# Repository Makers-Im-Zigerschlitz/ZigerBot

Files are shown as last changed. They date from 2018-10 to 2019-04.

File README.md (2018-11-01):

# ZigerBot

Arduino shield to teach STEM / basic robotics

Current state: _planning_ 

## Goal

Create an Arduino(R) shield to help teach STEM / basic robotics

## General idea

We love teaching about mechanics, electricity, electronics and robotics. ZigerBot allows us to have a robust platform to teach the very basic of all this. Participants build their own robotic platform, solder the ZigerBot shield and connect both. ZigerBot can then be programmed via Arduino IDE or ArduBlockly .

## Inspiration
https://github.com/FuzzyNoodle/Fuzzy-Naked-Mega

## Features for first iteration
- Arduino compatible with Atmega2560 and CP2102
- Power-Input: Drives ZigerBot and powers Arduino
- Drives two DC motors, connect with screw terminals (DRV8833PW)
- Prepared for 1-2 Ultrasonic Range Sensor (SR04)
- Has an RGB LED matrix (5x5 or bigger, WS2812B)
- Can play simple melodies or signal tones
- Has 4 tactile button inputs
- Has 1-2 potentiometers
- Has 4 Servo Outputs

## Dependencies
- FastLED Library
- Arduino Bootloader

## Pin Configuration

We try to minimalize conflicts with different in- and output components and their libraries. 

# ZigerBot

Arduino shield to teach STEM / basic robotics

Current state: _planning_ 

## Goal

Create an Arduino(R) shield to help teach STEM / basic robotics

## General idea

We love teaching about mechanics, electricity, electronics and robotics. ZigerBot allows us to have a robust platform to teach the very basic of all this. Participants build their own robotic platform, solder the ZigerBot shield and connect both. ZigerBot can then be programmed via Arduino IDE or ArduBlockly .

## Inspiration
https://github.com/FuzzyNoodle/Fuzzy-Naked-Mega

## Features for first iteration
- Arduino compatible with Atmega2560 and CP2102
- Power-Input: Drives ZigerBot and powers Arduino
- Drives two DC motors, connect with screw terminals
- Prepared for 1 Ultrasonic Range Sensor (SR04)
- Has an RGB LED matrix (5x5 or bigger, WS2812B)
- Can play simple melodies or signal tones
- Has 4 tactile button inputs
- Has 1-2 potentiometers
- Has 4 Servo Outputs

## Dependencies
- FastLED Library
- Arduino IDE, bootloader and generally Arduino libraries

## Pin Configuration

We try to minimalize conflicts with different in- and output components and their libraries. 

~ PWM

- Timer 0 is used by delay(), millis() and micros() - these functions are useful to beginners
- Timer 2 is used by the tone library
- Timer 5 is used by the servo/megaservo library for up to 12 servos

| Arduino IDE pin | ZigerBot | Special function |
| --- | --- | --- |
| D0 | not assigned | #f03c15Tx0 |
| D1 | not assigned | #f03c15Rx0 |
| D2~ | not assigned | #1589F0Timer 3 |
| D3~ | not assigned | #1589F0Timer 3 |
| D4~ | not assigned | #1589F0Timer 0 |
| D5~ | **Motor A Input 1** | #1589F0Timer 3 |
| D6~ | **Motor A Input 2** | #1589F0Timer 4 |
| D7~ | **Motor B Input 1** | #1589F0Timer 4 |
| D8~ | **Motor B Input 2** | #1589F0Timer 4 |
| D9~ | not assigned | #1589F0Timer 2 |
| D10~ | not assigned | #1589F0Timer 2 |
| D11~ | not assigned | #1589F0Timer 1 |
| D12~ | not assigned | #1589F0Timer 1 |
| D13~ | not assigned | #1589F0Timer 0, built-in LED|
| D14 | not assigned | #f03c15Tx3 |
| D15 | not assigned | #f03c15Rx3 |
| D16 | not assigned | #f03c15Tx2 |
| D17 | not assigned | #f03c15Rx2 |
| D18 | not assigned | #f03c15Tx1 |
| D19 | not assigned | #f03c15Rx1 |
| D20 | not assigned | #c5f015SDA |
| D21 | not assigned | #c5f015SCL |
| D22 | **Ultrasonic sensor SR04 trigger pin** | none |
| D23 | **Ultrasonic sensor SR04 echo pin** | none |
| D24 | **LED-Matrix data out** | none |
| D25 | **Piezo speaker** | none |
| D26 | **Tactile button 1** | none |
| D27 | **Tactile button 2** | none |
| D28 | **Tactile button 3** | none |
| D29 | **Tactile button 4** | none |
| D30 | **Servo 1** | none |
| D31 | **Servo 2** | none |
| D32 | **Servo 3** | none |
| D33 | **Servo 4** | none |
| D34 | not assigned | none |
| D35 | not assigned | none |
| D36 | not assigned | none |
| D37 | not assigned | none |
| D38 | not assigned | none |
| D39 | not assigned | none |
| D40 | not assigned | none |
| D41 | not assigned | none |
| D42 | not assigned | none |
| D43 | not assigned | none |
| D44~ | not assigned | #1589F0Timer 5 |
| D45~ | not assigned | #1589F0Timer 5 |
| D46~ | not assigned | #1589F0Timer 5 |
| D47 | not assigned | none |
| D48 | not assigned | none |
| D49 | not assigned | none |
| D50 | not assigned | #c5f015MISO |
| D51 | not assigned | #c5f015MOSI |
| D52 | not assigned | #c5f015SCK |
| D53 | not assigned | #c5f015SS |
| --- | --- | --- |
| A0 | **Potentiometer 1** | none |
| A1 | **Potentiometer 2** | none |
| A2 | not assigned | none |
| A3 | not assigned | none |
| A4 | not assigned | none |
| A5 | not assigned | none |
| A6 | not assigned | none |
| A7 | not assigned | none |
| A8 | not assigned | none |
| A9 | not assigned | none |
| A10 | not assigned | none |
| A11 | not assigned | none |
| A12 | not assigned | none |
| A13 | not assigned | none |
| A14 | not assigned | none |
| A15 | not assigned | none |

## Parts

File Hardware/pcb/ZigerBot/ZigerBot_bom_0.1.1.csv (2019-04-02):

Component | Description | Part | References | Value | Footprint | Quantity Per PCB | Datasheet | Digi-Key_PN | MPN | SKU | Category | Status | Family | DK_Datasheet_Link | DK_Detail_Page | Manufacturer
1 | Buzzer, polar | Buzzer | BZ1 | Buzzer CEM-1203(42) | BUZZER_CEM-1203(24)_12mm_6.5mm_0.6mm | 1 | ~ | 102-1153-ND
2 | Unpolarized capacitor | C_Small | C4 | 0.1 uF | C_0805 | 1 | ~ | 311-1141-1-ND
3 | Unpolarized capacitor | C | C1 C3 C8 C9 C10 C11 C12 C13 C14 C15 C16 C17 C18 C19 C20 C21 C23 C24 C25 C26 C27 C28 C29 C30 C31 C32 C33 C35 C36 C37 C38 C39 | 0.1uF | C_0805 | 32 | ~ | 311-1141-1-ND
4 | Unpolarized capacitor | C | C2 | 0.33uF | C_0805 | 1 | ~ | 311-3385-1-ND
5 | Unpolarized capacitor | C_Small | C5 C6 C7 | 10uF 16V | C_0805 | 3 | ~ | 490-3886-1-ND
6 | Unpolarized capacitor | C | C22 C34 | 4.7uF | C_0805 | 2 | ~ | 311-1863-1-ND
7 | LED dual, 2pin version | LED_Dual_2pin | D2 D3 | LED_Dual_2pin | LED_D5.0mm | 2 | ~ | 160-1038-ND | LTL-293SJW
8 | LED generic | LED | D5 | SMD LED green FAULT | LED_0603 | 1 |  | 160-1435-1-ND
9 | LED generic | LED | D1 | SMD LED red | LED_0603 | 1 |  | 160-1436-1-ND
10 | LED generic | LED | D4 | SMD LED yellow | LED_0603 | 1 |  | 160-1437-1-ND
11 | TVS Diode Array, 5.5V Standoff, 3 Channels, SOT-143 package | SP0503BAHT | D23 | SP0503BAHT | SOT-143_Handsoldering | 1 | http://www.littelfuse.com/~/media/files/littelfuse/technical%20resources/documents/data%20sheets/sp05xxba.pdf | F2715CT-ND
12 | RGB LED with integrated controller | WS2812B | D8 D9 D10 D11 D12 D13 D14 D15 D16 D17 D18 D19 D20 D21 D22 D24 D25 D26 D27 D28 D29 D30 D31 D32 D33 | WS2812B | LED_WS2812B-PLCC4 | 25 | https://cdn-shop.adafruit.com/datasheets/WS2812B.pdf | 1528-1104-ND
13 | Generic connector, single row, 01x03, script generated (kicad-library-utils/schlib/autogen/connector/) | Conn_01x03_Female | J6 J7 J8 J9 | 3 Pin Male Servo Header | Pin_Header_Straight_1x03_Pitch2.54mm | 4 | ~ | 732-5316-ND
14 |  | DIP-BLACK-MALE-HEADER-VERT_4P-2.54_ | J4 | 4 Pin Male SR-04 Header | H4-2.54 | 1 |  | 732-5317-ND | P125-1104A0BS116A1 | 320020017
15 | Generic connector, double row, 02x03, top/bottom pin numbering scheme (row 1: 1...pins_per_row, row2: pins_per_row+1 ... num_pins), script generated (kicad-library-utils/schlib/autogen/connector/) | Conn_02x03_Top_Bottom | J10 | ICSP | ICSP | 1 | ~ | 609-3218-ND
16 |  | SCREW-TERMINAL-GREEN_2P-5.0_ | J2 | M Power | H2-5.0-10.5X8.0MM | 1 |  | ED2609-ND |  | 320110031
17 |  | SCREW-TERMINAL-GREEN_2P-5.0_ | J1 | Motor A | H2-5.0-10.5X8.0MM | 1 |  | ED2609-ND |  | 320110031
18 |  | SCREW-TERMINAL-GREEN_2P-5.0_ | J3 | Motor B | H2-5.0-10.5X8.0MM | 1 |  | ED2609-ND |  | 320110031
19 | USB Micro Type B connector | USB_B_Micro | J5 | USB_B_Micro | USB_Micro-B_Molex-105017-0001 | 1 | ~ | 609-4616-1-ND
20 | Dual Jumper, normally closed | Jumper_NC_Dual | JP1 | Jumper | Pin_Header_Straight_1x03_Pitch2.54mm | 1 | ~ | 732-5316-ND
21 |  | SMD-MOSFET-P-CH-20V-2A-FDN340P_SOT-23_ | Q1 | SMD-MOSFET-P-CH-20V-2A-FDN340P_SOT-23_ | SOT-23 | 1 |  | FDN340PCT-ND | FDN340P | 305030026
22 | Resistor, small symbol | R_Small | R7 R8 | 0.2 Ohm | R_0805 | 2 | ~ | 311-.20SCT-ND
23 |  | SMD-RES-100R-5%-1_8W_0805_ | R1 | 100 Ohm | R_0805 | 1 |  | 311-100CRCT-ND |  | 301010319
24 |  | SMD-RES-1K-5%-1_8W_0805_ | R2 R3 R6 R9 | 10k | R_0805 | 4 |  | 311-10.0KCRCT-ND |  | 301010311
25 |  | SMD-RES-1K-5%-1_8W_0805_ | R4 R10 R12 | 1k | R_0805 | 3 |  | 311-1.00KCRCT-ND |  | 301010311
26 |  | SMD-RES-100R-5%-1_8W_0805_ | R5 | 470 Ohm | R_0805 | 1 |  | 311-470CRCT-ND |  | 301010319
27 | Potentiometer | R_POT | RV1 RV2 | Potentiometer | Potentiometer_Trimmer-EVM3E | 2 | ~ | 1528-1997-ND
28 | Single Pole Single Throw (SPST) switch | SW_SPST | SW1 SW2 SW3 SW4 | SMD Button | SW_SPST_SKQG | 4 |  | CKN9087CT-ND | PTS645SK50SMTR92 LFS | 311020017
29 | 16MHz, 256kB Flash, 8kB SRAM, 4kB EEPROM, JTAG, TQFP-100 | ATmega2560-16AU | U3 | ATmega2560-16AU | TQFP-100_14x14mm_Pitch0.5mm | 1 | http://ww1.microchip.com/downloads/en/DeviceDoc/Atmel-2549-8-bit-AVR-Microcontroller-ATmega640-1280-1281-2560-2561_datasheet.pdf | ATMEGA2560-16AU-ND
30 | USB to UART master bridge | CP2102N-A01-GQFN24 | U4 | CP2102N-A01-GQFN24 | QFN-24-1EP_4x4mm_Pitch0.5mm | 1 | http://www.silabs.com/support%20documents/technicaldocs/cp2102n-datasheet.pdf | 336-4737-1-ND
31 | IC MOTOR DRIVER PAR 16HTSSOP | DRV8833PWPR | U2 | DRV8833PWPR | TSSOP-16-1EP_W4.40mm | 1 | http://www.ti.com/lit/ds/symlink/drv8833.pdf | 296-29434-1-ND | DRV8833PWPR |  | Integrated Circuits (ICs) | Active | PMIC - Full, Half-Bridge Drivers | http://www.ti.com/lit/ds/symlink/drv8833.pdf | /product-detail/en/texas-instruments/DRV8833PWPR/296-29434-1-ND/2743171 | Texas Instruments
32 | Positive 1.5A 35V Linear Regulator, Fixed Output 5V, TO-220/TO-263/TO-252 | L7805 | U1 | L7805CDT-TR | TO-252-2 | 1 | http://www.st.com/content/ccc/resource/technical/document/datasheet/41/4f/b3/b0/12/d4/47/88/CD00000444.pdf/files/CD00000444.pdf/jcr:content/translations/en.CD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 | 497-7255-1-ND | L7805CDT-TR | 310030010
33 | Three pin ceramic resonator | Resonator_Small | Y1 | 16MHz Resonator | Resonator_SMD_muRata_CSTNE16M0V530000_3pin_3.2x1.3x0.9mm | 1 | ~ | CSTNE16M0V53C000R0
Component Groups: | 33
Component Count: | 105
Fitted Components: | 105
Number of PCBs: | 1
Total components: | 105
Schematic Version: | 0.1.1
Schematic Date: | 2018-10-10
BoM Date: | 16/01/2019 02:12:57
Schematic Source: | C:\Users\Mike\Documents\GitHub\ZigerBot\Hardware\pcb\ZigerBot\ZigerBot.sch
KiCad Version: | Eeschema (5.0.0)

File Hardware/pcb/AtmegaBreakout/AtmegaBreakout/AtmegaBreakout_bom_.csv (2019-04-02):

Component | Description | Part | References | Value | Footprint | Quantity Per PCB | Datasheet | MPN | Digi-Key_PN | Category | Status | Family | DK_Datasheet_Link | DK_Detail_Page | Manufacturer
1 | Unpolarized capacitor | C_Small | C1 C2 C3 C4 C5 C6 C8 | 0.1uF | C_0805_HandSoldering | 7 | ~ | CC0805ZRY5V9BB104 | 311-1361-1-ND
2 | Unpolarized capacitor | C_Small | C7 | 4.7uF | C_0805_HandSoldering | 1 | ~ | CC0805ZRY5V6BB475 | 311-1371-1-ND
3 | LED, small symbol | LED_Small | D2 | LED L | LED_0805_HandSoldering | 1 | ~ | LTST-C170GKT | 160-1179-1-ND
4 | LED, small symbol | LED_Small | D1 | LED USB Rx | LED_0805_HandSoldering | 1 | ~ | LTST-C171KSKT | 160-1428-1-ND
5 | LED, small symbol | LED_Small | D4 | LED USB Tx | LED_0805_HandSoldering | 1 | ~ | LTST-C171KSKT | 160-1428-1-ND
6 | TVS DIODE 5.5V 8.5V SOT143-4 | SP0503BAHTG | D3 | SP0503BAHTG | SOT-143-4 | 1 | http://www.littelfuse.com/~/media/files/littelfuse/technical%20resources/documents/data%20sheets/sp05xxba.pdf | SP0503BAHTG | F2715CT-ND | Circuit Protection | Active | TVS - Diodes | http://www.littelfuse.com/~/media/files/littelfuse/technical%20resources/documents/data%20sheets/sp05xxba.pdf | /product-detail/en/littelfuse-inc/SP0503BAHTG/F2715CT-ND/1154322 | Littelfuse Inc.
7 | Generic connector, double row, 02x08, odd/even pin numbering scheme (row 1 odd numbers, row 2 even numbers), script generated (kicad-library-utils/schlib/autogen/connector/) | Conn_02x08_Odd_Even | J1 | ANALOG | Pin_Header_Straight_2x08_Pitch2.54mm | 1 | ~ | 68602-116HLF | 609-3364-ND
8 | Generic connector, double row, 02x08, odd/even pin numbering scheme (row 1 odd numbers, row 2 even numbers), script generated (kicad-library-utils/schlib/autogen/connector/) | Conn_02x08_Odd_Even | J3 | DIGITAL1 | Pin_Header_Straight_2x08_Pitch2.54mm | 1 | ~ | 68602-116HLF | 609-3364-ND
9 | Generic connector, double row, 02x08, odd/even pin numbering scheme (row 1 odd numbers, row 2 even numbers), script generated (kicad-library-utils/schlib/autogen/connector/) | Conn_02x08_Odd_Even | J4 | DIGITAL2 | Pin_Header_Straight_2x08_Pitch2.54mm | 1 | ~ | 68602-116HLF | 609-3364-ND
10 | Generic connector, double row, 02x08, odd/even pin numbering scheme (row 1 odd numbers, row 2 even numbers), script generated (kicad-library-utils/schlib/autogen/connector/) | Conn_02x08_Odd_Even | J5 | DIGITAL3 | Pin_Header_Straight_2x08_Pitch2.54mm | 1 | ~ | 68602-116HLF | 609-3364-ND
11 | Generic connector, double row, 02x08, odd/even pin numbering scheme (row 1 odd numbers, row 2 even numbers), script generated (kicad-library-utils/schlib/autogen/connector/) | Conn_02x08_Odd_Even | J2 | POWER and COMMS | Pin_Header_Straight_2x08_Pitch2.54mm | 1 | ~ | 68602-116HLF | 609-3364-ND
12 | USB Micro Type B connector | USB_B_Micro | J6 | USB_B_Micro | USB_Micro-B_Molex_47346-0001 | 1 | ~ | 47346-0001 | WM17141CT-ND
13 | Resistor | R | R2 R3 R4 R7 | 1k | R_0805_HandSoldering | 4 | ~ | RC0805FR-071KL | 311-1.00KCRCT-ND
14 | Resistor | R | R5 | 22.1k | R_0805_HandSoldering | 1 | ~ | RC0805FR-0722K1L | 311-22.1KCRCT-ND
15 | Resistor | R | R6 | 47.5k | R_0805_HandSoldering | 1 | ~ | RC0805FR-0747K5L | 311-47.5KCRCT-ND
16 | Resistor | R | R1 | 47k | R_0805_HandSoldering | 1 | ~ | RC0805FR-0747KL | 311-47.0KCRCT-ND
17 | Push button switch, generic, two pins | SW_Push | SW1 | EVP-ASAC1A | EVP-ASAC1A | 1 |  | EVP-ASAC1A | P16854CT-ND
18 | IC MCU 8BIT 256KB FLASH 100TQFP | ATMEGA2560-16AU | U1 | ATMEGA2560-16AU | TQFP-100_14x14mm | 1 | http://ww1.microchip.com/downloads/en/DeviceDoc/Atmel-2549-8-bit-AVR-Microcontroller-ATmega640-1280-1281-2560-2561_Summary.pdf | ATMEGA2560-16AU | ATMEGA2560-16AU-ND | Integrated Circuits (ICs) | Active | Embedded - Microcontrollers | http://ww1.microchip.com/downloads/en/DeviceDoc/Atmel-2549-8-bit-AVR-Microcontroller-ATmega640-1280-1281-2560-2561_Summary.pdf | /product-detail/en/microchip-technology/ATMEGA2560-16AU/ATMEGA2560-16AU-ND/735455 | Microchip Technology
19 | USB to UART master bridge | CP2102N-A01-GQFN24 | U2 | CP2102N-A01-GQFN24 | QFN-24-1EP_4x4mm_Pitch0.5mm | 1 | http://www.silabs.com/support%20documents/technicaldocs/cp2102n-datasheet.pdf | CP2102N-A01-GQFN24 | 336-4737-1-ND
20 | Three pin ceramic resonator | Resonator | Y1 | 16MHz Ceramic Resonator | AWSCR-MT | 1 | ~ | AWSCR-16.00MTD-T | 535-9362-1-ND
Component Groups: | 20
Component Count: | 29
Fitted Components: | 29
Number of PCBs: | 1
Total components: | 29
Schematic Version:
Schematic Date:
BoM Date: | 27/01/2019 21:54:11
Schematic Source: | C:\Users\Mike\Documents\GitHub\ZigerBot\Hardware\pcb\AtmegaBreakout\AtmegaBreakout\AtmegaBreakout.sch
KiCad Version: | Eeschema (5.0.0)

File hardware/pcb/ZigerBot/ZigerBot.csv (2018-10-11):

Part/Designator | Manufacture Part Number/Seeed SKU | Quantity
R1,R2,R3,R4,R5,R6,R7,R8 | 301010311 | 8
C1,C2 | 302010165 | 2
D3,D4,D5,D6,D9,D10,D11,D12 | 304020027 | 8
D1,D2,D7,D8,D13,D14,D15,D16 | 304090046 | 8
U4 | 310010006 | 1
U1 | 310030010 | 1
U3 | 310040018 | 1
J4 | 320020016 | 1
J1 | 320110029 | 1
J2,J3 | 320110031 | 2
U2 | 74HCU04D | 1
U5 | CP2102N-A01-GQFN20 | 1

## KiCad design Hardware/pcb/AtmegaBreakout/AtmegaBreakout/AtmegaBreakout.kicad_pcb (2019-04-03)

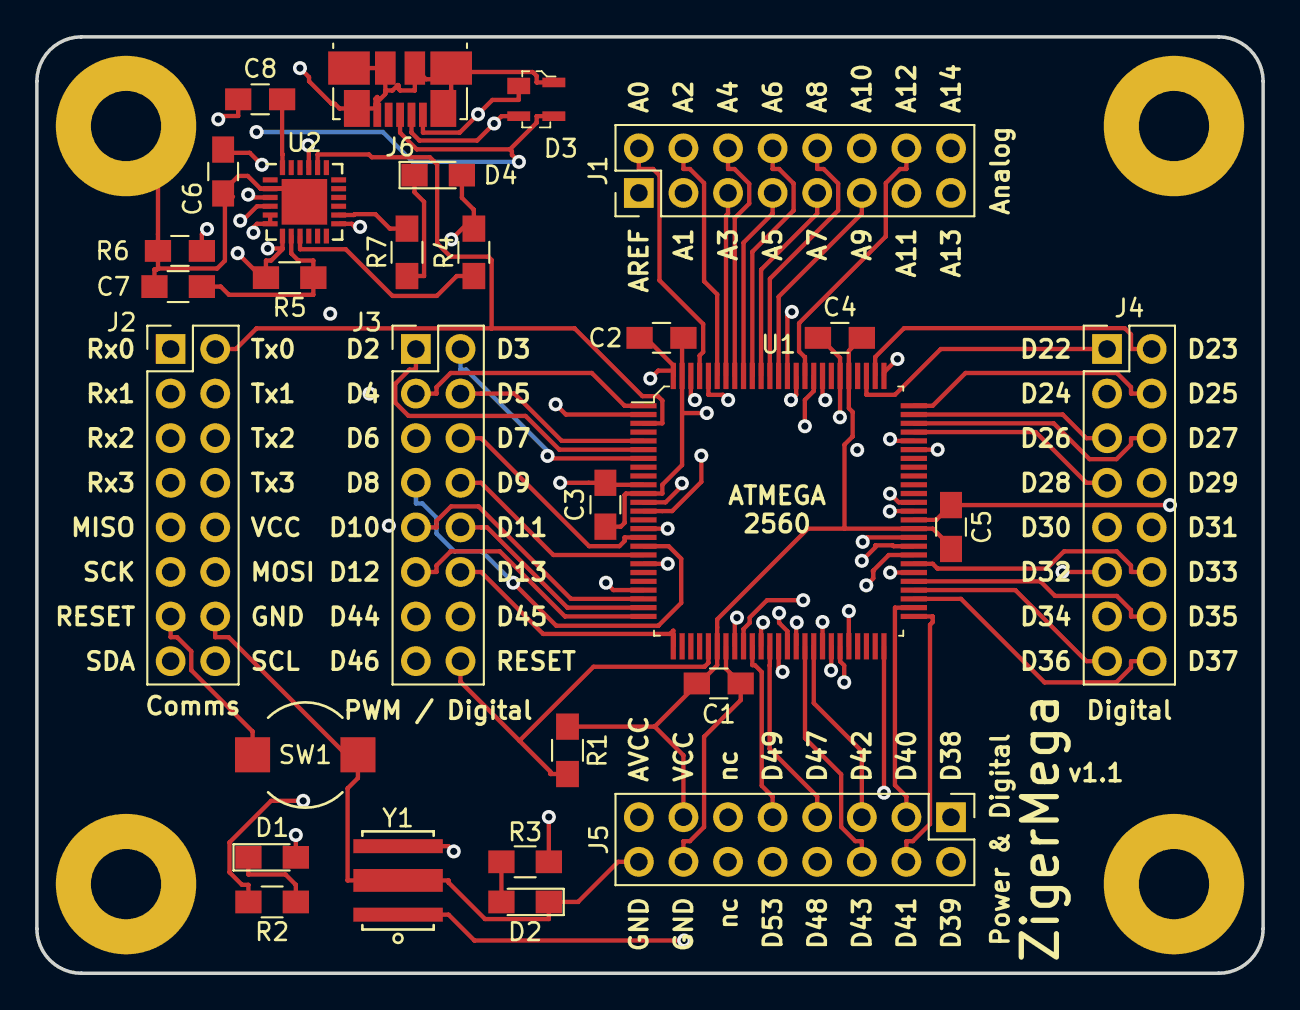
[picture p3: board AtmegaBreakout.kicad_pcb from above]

Board: 4 copper layers, 69.9 x 53.3 mm, 33 parts (0 on the bottom side), 85 nets.

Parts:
C1, C2, C3, C4, C5, C6, C8: 0.1uF; C_0805_HandSoldering
C7: 4.7uF; C_0805_HandSoldering
D1: LED USB Rx; LED_0805_HandSoldering
D2: LED L; LED_0805_HandSoldering
D3: SP0503BAHTG; SOT-143-4
D4: LED USB Tx; LED_0805_HandSoldering
J1: ANALOG; Pin_Header_Straight_2x08_Pitch2.54mm
J2: POWER and COMMS; Pin_Header_Straight_2x08_Pitch2.54mm
J3: DIGITAL1; Pin_Header_Straight_2x08_Pitch2.54mm
J4: DIGITAL2; Pin_Header_Straight_2x08_Pitch2.54mm
J5: DIGITAL3; Pin_Header_Straight_2x08_Pitch2.54mm
J6: USB_B_Micro; USB_Micro-B_Molex_47346-0001
MH1, MH2, MH3, MH4: MountingHole_Pad; MountingHole_4mm_Pad
R1: 47k; R_0805_HandSoldering
R2, R3, R4, R7: 1k; R_0805_HandSoldering
R5: 22.1k; R_0805_HandSoldering
R6: 47.5k; R_0805_HandSoldering
SW1: EVP-ASAC1A
U1: ATMEGA2560-16AU; TQFP-100_14x14mm
U2: CP2102N-A01-GQFN24; QFN-24-1EP_4x4mm_Pitch0.5mm
Y1: 16MHz Ceramic Resonator; AWSCR-MT

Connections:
/A0: J1.2, U1.97
/A1: J1.3, U1.96
/A2: J1.4, U1.95
/A3: J1.5, U1.94
/A4: J1.6, U1.93
/A5: J1.7, U1.92
/A6: J1.8, U1.91
/A7: J1.9, U1.90
/A8: J1.10, U1.89
/A9: J1.11, U1.88
/A10: J1.12, U1.87
/A11: J1.13, U1.86
/A12: J1.14, U1.85
/A13: J1.15, U1.84
/A14: J1.16, U1.83
/AREF: J1.1, U1.98
/AVCC: C2.2, J5.15, U1.100
/D2: J3.1, U1.6
/D3: J3.2, U1.7
/D4: J3.3, U1.1
/D5: J3.4, U1.5
/D6: J3.5, U1.15
/D7: J3.6, U1.16
/D8: J3.7, U1.17
/D9: J3.8, U1.18
/D10: J3.9, U1.23
/D11: J3.10, U1.24
/D12: J3.11, U1.25
/D13: J3.12, R3.2, U1.26
/D22: J4.1, U1.78
/D23: J4.2, U1.77
/D24: J4.3, U1.76
/D25: J4.4, U1.75
/D26: J4.5, U1.74
/D27: J4.6, U1.73
/D28: J4.7, U1.72
/D29: J4.8, U1.71
/D30: J4.9, U1.60
/D31: J4.10, U1.59
/D32: J4.11, U1.58
/D33: J4.12, U1.57
/D34: J4.13, U1.56
/D35: J4.14, U1.55
/D36: J4.15, U1.54
/D37: J4.16, U1.53
/D38: J5.1, U1.50
/D39: J5.2, U1.70
/D40: J5.3, U1.52
/D41: J5.4, U1.51
/D42: J5.5, U1.42
/D43: J5.6, U1.41
/D44: J3.13, U1.40
/D45: J3.14, U1.39
/D46: J3.15, U1.38
/D47: J5.7, U1.37
/D48: J5.8, U1.36
/D49: J5.9, U1.35
/D53-SS: J5.10, U1.19
/DTR: C8.2, U2.24
/MISO-D50: J2.9, U1.22
/RESET: C8.1, J2.13, J3.16, R1.2, SW1.1, U1.30
/Rx0-D0: J2.1, U1.2, U2.21
/Rx1-D19: J2.3, U1.45
/Rx2-D17: J2.5, U1.12
/Rx3-D15: J2.7, U1.63
/SCL-D21: J2.16, U1.43
/SDA-D20: J2.15, U1.44
/Tx0-D1: J2.2, U1.3, U2.20
/Tx1-D18: J2.4, U1.46
/Tx2-D16: J2.6, U1.13
/Tx3-D14: J2.8, U1.64
/VIO: C6.2, C7.1, D1.2, D4.2, R4.2, U2.5, U2.6
/XTAL1: U1.34, Y1.3
/XTAL2: U1.33, Y1.1
GND: C1.1, C2.1, C3.1, C4.1, C5.1, C6.1, C7.2, D2.1, D3.1, J2.14, J5.14, J5.16, J6.5, J6.6, MH1.1, MH2.1, MH3.1, MH4.1, R6.1, SW1.2, U1.11, U1.32, U1.62, U1.81, U1.99, U2.2, U2.25, Y1.2
unnamed: D1.1, R2.1
unnamed: D2.2, R3.1
unnamed: D3.3, J6.2, U2.4
unnamed: D3.4, J6.3, U2.3
unnamed: D4.1, R7.1
unnamed: R2.2, U2.13
unnamed: R4.1, U2.9
unnamed: R5.1, R6.2, U2.8
unnamed: R7.2, U2.14
VCC: C1.2, C3.2, C4.2, C5.2, D3.2, J2.10, J5.13, J6.1, R1.1, R5.2, U1.10, U1.31, U1.61, U1.80, U2.7

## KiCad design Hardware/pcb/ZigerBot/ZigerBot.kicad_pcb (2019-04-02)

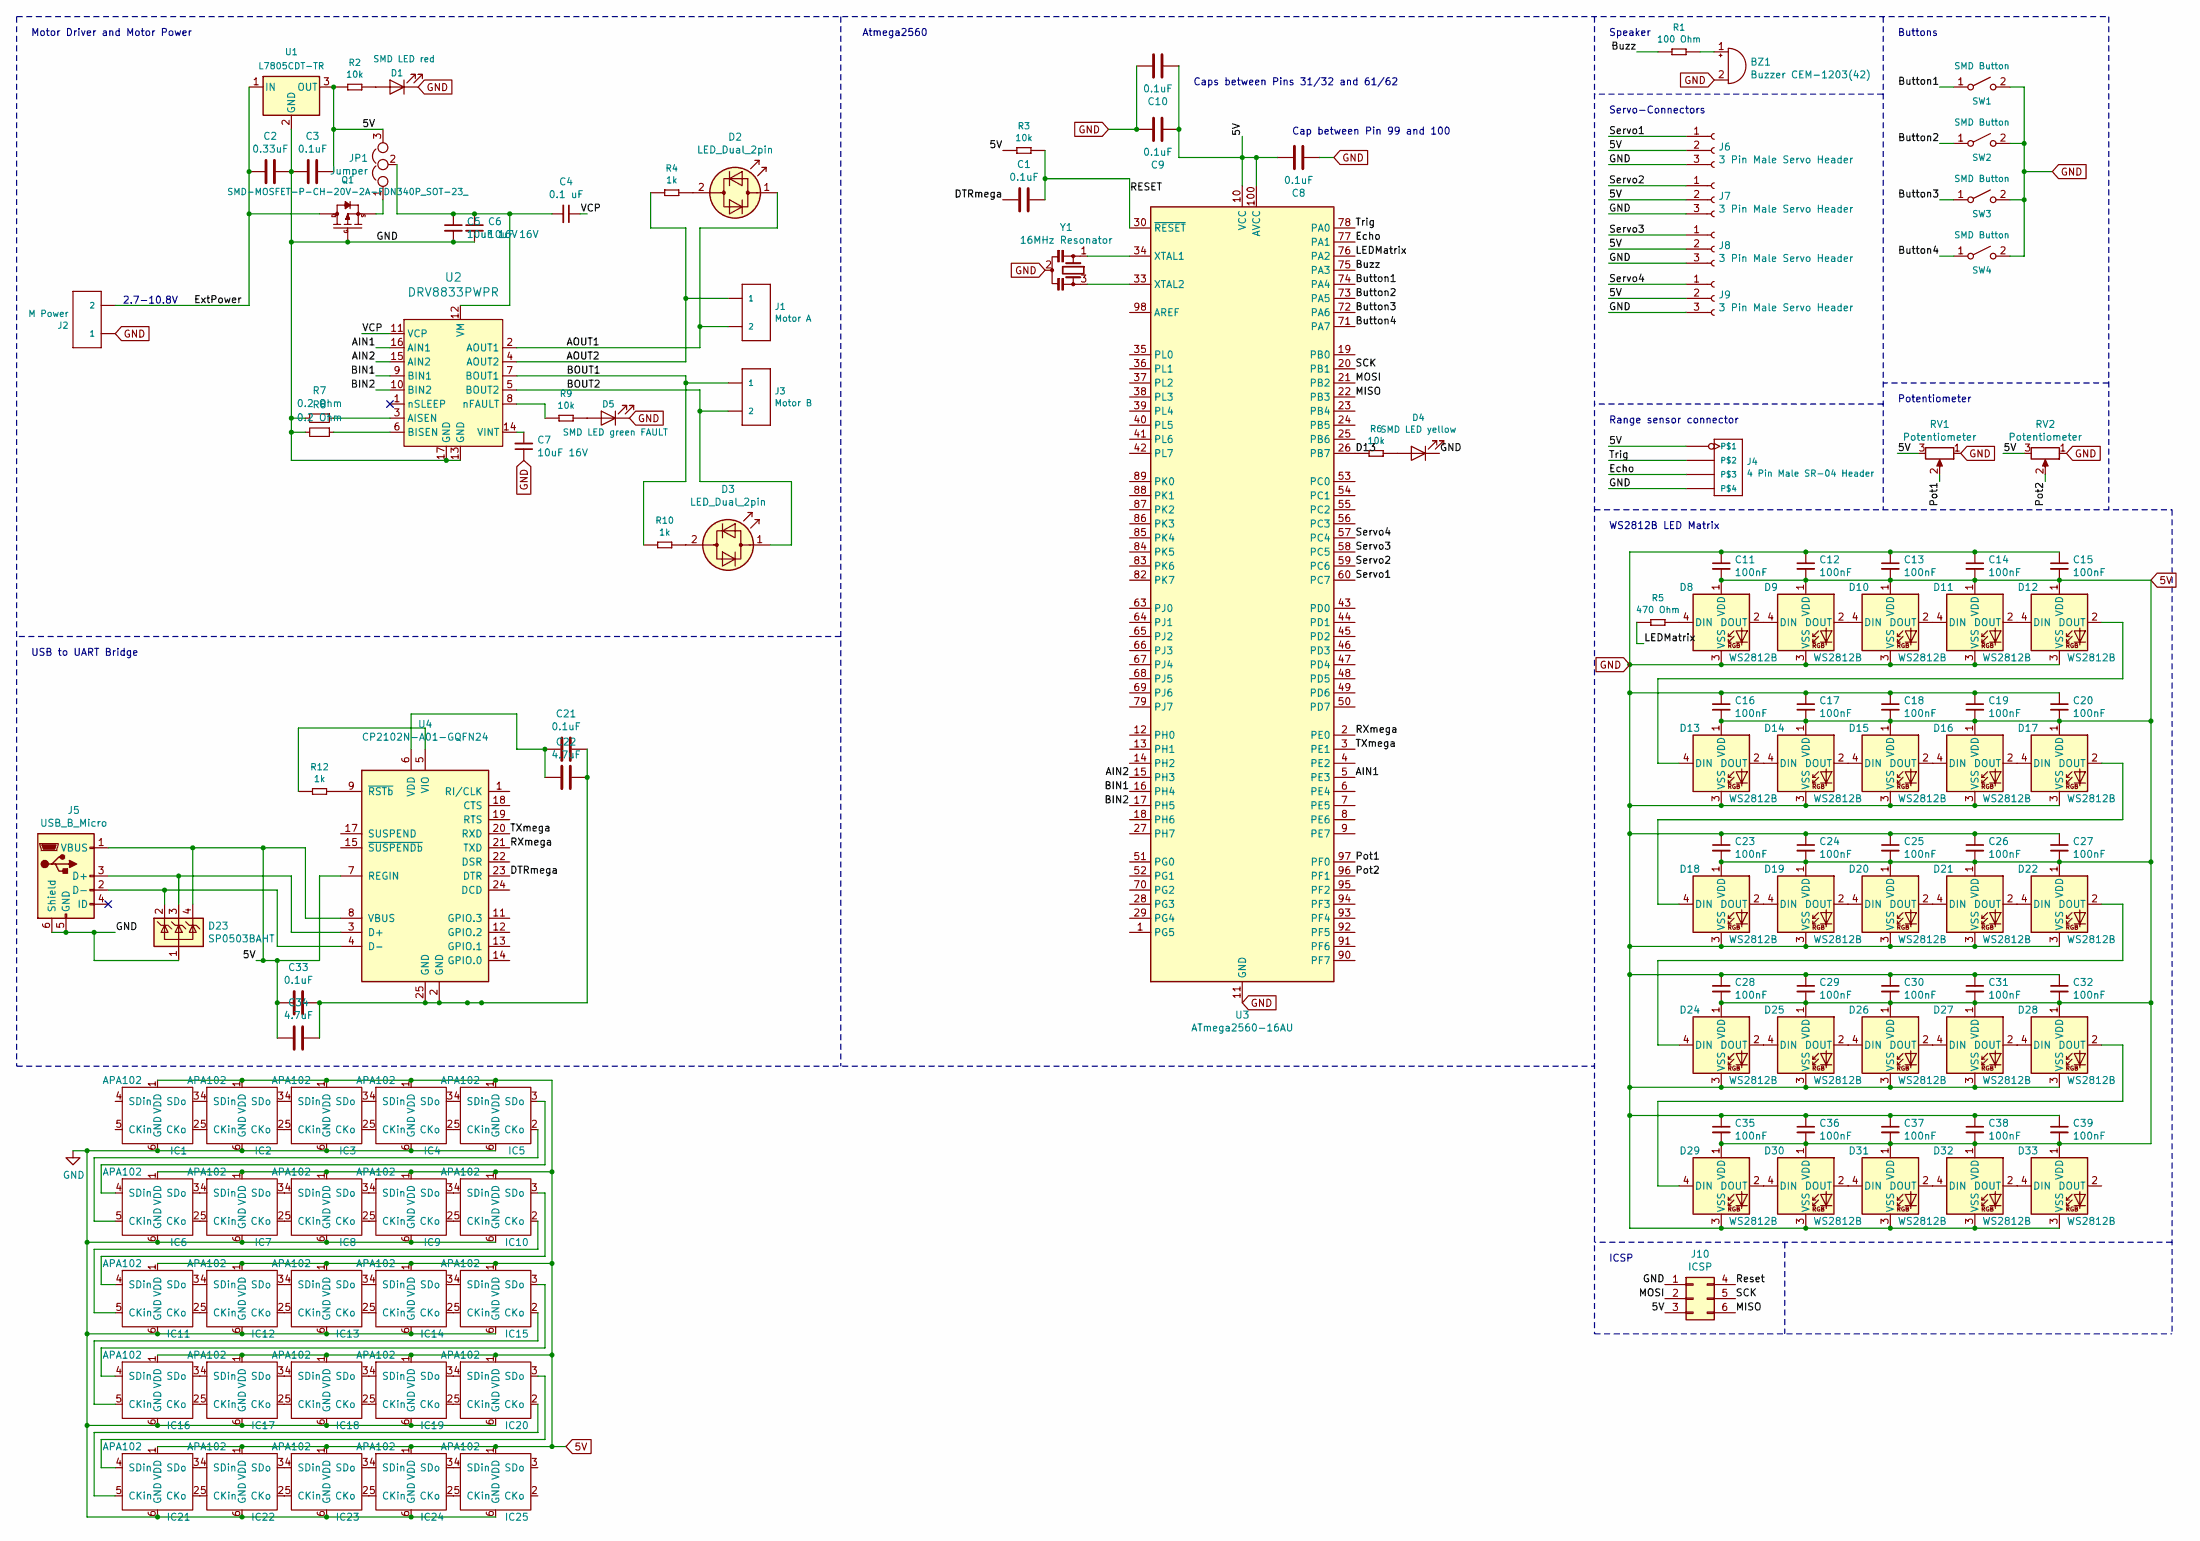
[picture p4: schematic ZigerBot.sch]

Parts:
BZ1: Buzzer CEM-1203(42); BUZZER_CEM-1203(24)_12mm_6.5mm_0.6mm; Digi-Key_PN 102-1153-ND
C1, C3, C8, C9, C10, C21, C33: 0.1uF; C_0805; Digi-Key_PN 311-1141-1-ND
C2: 0.33uF; C_0805; Digi-Key_PN 311-3385-1-ND
C4: 0.1 uF; C_0805; Digi-Key_PN 311-1141-1-ND
C5, C6, C7: 10uF 16V; C_0805; Digi-Key_PN 490-3886-1-ND
C11, C12, C13, C14, C15, C16, C17, C18, C19, C20, C23, C24, C25, C26, C27, C28, C29, C30, C31, C32, C35, C36, C37, C38, C39: 100nF; C_0805; Digi-Key_PN 311-1141-1-ND
C22, C34: 4.7uF; C_0805; Digi-Key_PN 311-1863-1-ND
D1: SMD LED red; LED_0603; Digi-Key_PN 160-1436-1-ND
D2, D3: LED_Dual_2pin; LED_D5.0mm; MPN LTL-293SJW; Digi-Key_PN 160-1038-ND
D4: SMD LED yellow; LED_0603; Digi-Key_PN 160-1437-1-ND
D5: SMD LED green FAULT; LED_0603; Digi-Key_PN 160-1435-1-ND
D8, D9, D10, D11, D12, D13, D14, D15, D16, D17, D18, D19, D20, D21, D22, D24, D25, D26, D27, D28, D29, D30, D31, D32, D33: WS2812B; LED_WS2812B-PLCC4; Digi-Key_PN 1528-1104-ND
D23: SP0503BAHT; SOT-143_Handsoldering; Digi-Key_PN F2715CT-ND
IC1, IC2, IC3, IC4, IC5, IC6, IC7, IC8, IC9, IC10, IC11, IC12, IC13, IC14, IC15, IC16, IC17, IC18, IC19, IC20, IC21, IC22, IC23, IC24, IC25: APA102; APA102-2020
J1: Motor A; H2-5.0-10.5X8.0MM; Digi-Key_PN ED2609-ND
J2: M Power; H2-5.0-10.5X8.0MM; Digi-Key_PN ED2609-ND
J3: Motor B; H2-5.0-10.5X8.0MM; Digi-Key_PN ED2609-ND
J4: 4 Pin Male SR-04 Header; H4-2.54; MPN P125-1104A0BS116A1; Digi-Key_PN 732-5317-ND
J5: USB_B_Micro; USB_Micro-B_Molex-105017-0001; Digi-Key_PN 609-4616-1-ND
J6, J7, J8, J9: 3 Pin Male Servo Header; Pin_Header_Straight_1x03_Pitch2.54mm; Digi-Key_PN 732-5316-ND
J10: ICSP; Digi-Key_PN 609-3218-ND
JP1: Jumper; Pin_Header_Straight_1x03_Pitch2.54mm; Digi-Key_PN 732-5316-ND
Q1: SMD-MOSFET-P-CH-20V-2A-FDN340P_SOT-23_; SOT-23; MPN FDN340P; Digi-Key_PN FDN340PCT-ND
R1: 100 Ohm; R_0805; Digi-Key_PN 311-100CRCT-ND
R2, R3, R6, R9: 10k; R_0805; Digi-Key_PN 311-10.0KCRCT-ND
R4, R10, R12: 1k; R_0805; Digi-Key_PN 311-1.00KCRCT-ND
R5: 470 Ohm; R_0805; Digi-Key_PN 311-470CRCT-ND
R7, R8: 0.2 Ohm; R_0805; Digi-Key_PN 311-.20SCT-ND
RV1, RV2: Potentiometer; Potentiometer_Trimmer-EVM3E; Digi-Key_PN 1528-1997-ND
SW1, SW2, SW3, SW4: SMD Button; SW_SPST_SKQG; MPN PTS645SK50SMTR92 LFS; Digi-Key_PN CKN9087CT-ND
U1: L7805CDT-TR; TO-252-2; MPN L7805CDT-TR; Digi-Key_PN 497-7255-1-ND
U2: DRV8833PWPR; TSSOP-16-1EP_W4.40mm; MPN DRV8833PWPR; Digi-Key_PN 296-29434-1-ND
U3: ATmega2560-16AU; TQFP-100_14x14mm_Pitch0.5mm; Digi-Key_PN ATMEGA2560-16AU-ND
U4: CP2102N-A01-GQFN24; QFN-24-1EP_4x4mm_Pitch0.5mm; Digi-Key_PN 336-4737-1-ND
Y1: 16MHz Resonator; Resonator_SMD_muRata_CSTNE16M0V530000_3pin_3.2x1.3x0.9mm; Digi-Key_PN CSTNE16M0V53C000R0

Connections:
5V: C3.1, C8.1, C9.2, C10.2, C11.2, C12.2, C13.2, C14.2, C15.2, C16.2, C17.2, C18.2, C19.2, C20.2, C23.2, C24.2, C25.2, C26.2, C27.2, C28.2, C29.2, C30.2, C31.2, C32.2, C33.2, C34.2, C35.2, C36.2, C37.2, C38.2, C39.2, D8.1 (VDD), D9.1 (VDD), D10.1 (VDD), D11.1 (VDD), D12.1 (VDD), D13.1 (VDD), D14.1 (VDD), D15.1 (VDD), D16.1 (VDD), D17.1 (VDD), D18.1 (VDD), D19.1 (VDD), D20.1 (VDD), D21.1 (VDD), D22.1 (VDD), D23.4 (K), D24.1 (VDD), D25.1 (VDD), D26.1 (VDD), D27.1 (VDD), D28.1 (VDD), D29.1 (VDD), D30.1 (VDD), D31.1 (VDD), D32.1 (VDD), D33.1 (VDD), IC1.1 (VDD), IC2.1 (VDD), IC3.1 (VDD), IC4.1 (VDD), IC5.1 (VDD), IC6.1 (VDD), IC7.1 (VDD), IC8.1 (VDD), IC9.1 (VDD), IC10.1 (VDD), IC11.1 (VDD), IC12.1 (VDD), IC13.1 (VDD), IC14.1 (VDD), IC15.1 (VDD), IC16.1 (VDD), IC17.1 (VDD), IC18.1 (VDD), IC19.1 (VDD), IC20.1 (VDD), IC21.1 (VDD), IC22.1 (VDD), IC23.1 (VDD), IC24.1 (VDD), IC25.1 (VDD), J4.1, J5.1 (VBUS), J6.2, J7.2, J8.2, J9.2, J10.3, JP1.3, R2.1, R3.1, RV1.3, RV2.3, U1.3 (OUT), U3.10 (VCC), U3.31 (VCC), U3.61 (VCC), U3.80 (VCC), U3.100 (AVCC), U4.7 (REGIN), U4.8 (VBUS)
/AIN1: U2.16 (AIN1), U3.5 (PE3)
/AIN2: U2.15 (AIN2), U3.15 (PH3)
/AOUT1: D2.1 (KA), J1.2, U2.2 (AOUT1)
/AOUT2: J1.1, R4.1, U2.4 (AOUT2)
/BIN1: U2.9 (BIN1), U3.16 (PH4)
/BIN2: U2.10 (BIN2), U3.17 (PH5)
/BOUT1: J3.1, R10.1, U2.7 (BOUT1)
/BOUT2: D3.1 (KA), J3.2, U2.5 (BOUT2)
/Button1: SW1.1 (A), U3.74 (PA4)
/Button2: SW2.1 (A), U3.73 (PA5)
/Button3: SW3.1 (A), U3.72 (PA6)
/Button4: SW4.1 (A), U3.71 (PA7)
/Buzz: R1.1, U3.75 (PA3)
/D13: R6.1, U3.26 (PB7)
/DTRmega: C1.2, U4.23 (DTR)
/Echo: J4.3, U3.77 (PA1)
/ExtPower: C2.2, J2.2, Q1.3 (D), U1.1 (IN)
/LEDMatrix: R5.1, U3.76 (PA2)
/MISO: J10.6, U3.22 (PB3)
/MOSI: J10.2, U3.21 (PB2)
/Pot1: RV1.2, U3.97 (PF0)
/Pot2: RV2.2, U3.96 (PF1)
/RESET: C1.1, R3.2, U3.30 (~RESET)
/RXmega: U3.2 (PE0), U4.21 (TXD)
/Reset: J10.4
/SCK: J10.5, U3.20 (PB1)
/Servo1: J6.1, U3.60 (PC7)
/Servo2: J7.1, U3.59 (PC6)
/Servo3: J8.1, U3.58 (PC5)
/Servo4: J9.1, U3.57 (PC4)
/TXmega: U3.3 (PE1), U4.20 (RXD)
/Trig: J4.2, U3.78 (PA0)
/VCP: C4.1, U2.11 (VCP)
GND: BZ1.2 (+), C2.1, C3.2, C5.2, C6.2, C7.1, C8.2, C9.1, C10.1, C11.1, C12.1, C13.1, C14.1, C15.1, C16.1, C17.1, C18.1, C19.1, C20.1, C23.1, C24.1, C25.1, C26.1, C27.1, C28.1, C29.1, C30.1, C31.1, C32.1, C35.1, C36.1, C37.1, C38.1, C39.1, D1.1 (K), D4.1 (K), D5.1 (K), D8.3 (VSS), D9.3 (VSS), D10.3 (VSS), D11.3 (VSS), D12.3 (VSS), D13.3 (VSS), D14.3 (VSS), D15.3 (VSS), D16.3 (VSS), D17.3 (VSS), D18.3 (VSS), D19.3 (VSS), D20.3 (VSS), D21.3 (VSS), D22.3 (VSS), D23.1 (A), D24.3 (VSS), D25.3 (VSS), D26.3 (VSS), D27.3 (VSS), D28.3 (VSS), D29.3 (VSS), D30.3 (VSS), D31.3 (VSS), D32.3 (VSS), D33.3 (VSS), IC1.6 (GND), IC2.6 (GND), IC3.6 (GND), IC4.6 (GND), IC5.6 (GND), IC6.6 (GND), IC7.6 (GND), IC8.6 (GND), IC9.6 (GND), IC10.6 (GND), IC11.6 (GND), IC12.6 (GND), IC13.6 (GND), IC14.6 (GND), IC15.6 (GND), IC16.6 (GND), IC17.6 (GND), IC18.6 (GND), IC19.6 (GND), IC20.6 (GND), IC21.6 (GND), IC22.6 (GND), IC23.6 (GND), IC24.6 (GND), IC25.6 (GND), J2.1, J4.4, J5.5 (GND), J5.6 (Shield), J6.3, J7.3, J8.3, J9.3, J10.1, Q1.1 (G), R7.2, R8.2, RV1.1, RV2.1, SW1.2 (B), SW2.2 (B), SW3.2 (B), SW4.2 (B), U1.2 (GND), U2.13 (GND), U2.17 (GND), U3.11 (GND), U3.32 (GND), U3.62 (GND), U3.81 (GND), U3.99 (GND), Y1.2
unnamed: BZ1.1 (-), R1.2
unnamed: C4.2, C5.1, C6.1, JP1.2, U2.12 (VM)
unnamed: C7.2, U2.14 (VINT)
unnamed: C21.1, C22.1, C33.1, C34.1, U4.2 (GND), U4.10 (NC), U4.16 (NC), U4.25 (GND)
unnamed: C21.2, C22.2, U4.6 (VDD)
unnamed: D1.2 (A), R2.2
unnamed: D2.2 (AK), R4.2
unnamed: D3.2 (AK), R10.2
unnamed: D4.2 (A), R6.2
unnamed: D5.2 (A), R9.2
unnamed: D8.2 (DOUT), D9.4 (DIN)
unnamed: D8.4 (DIN), R5.2
unnamed: D10.2 (DOUT), D11.4 (DIN)
unnamed: D9.2 (DOUT), D10.4 (DIN)
unnamed: D11.2 (DOUT), D12.4 (DIN)
unnamed: D12.2 (DOUT), D13.4 (DIN)
unnamed: D13.2 (DOUT), D14.4 (DIN)
unnamed: D14.2 (DOUT), D15.4 (DIN)
unnamed: D15.2 (DOUT), D16.4 (DIN)
unnamed: D16.2 (DOUT), D17.4 (DIN)
unnamed: D17.2 (DOUT), D18.4 (DIN)
unnamed: D18.2 (DOUT), D19.4 (DIN)
unnamed: D19.2 (DOUT), D20.4 (DIN)
unnamed: D20.2 (DOUT), D21.4 (DIN)
unnamed: D21.2 (DOUT), D22.4 (DIN)
unnamed: D22.2 (DOUT), D24.4 (DIN)
unnamed: D23.2 (K), J5.2 (D-), U4.4 (D-)
unnamed: D23.3 (K), J5.3 (D+), U4.3 (D+)
unnamed: D24.2 (DOUT), D25.4 (DIN)
unnamed: D25.2 (DOUT), D26.4 (DIN)
unnamed: D26.2 (DOUT), D27.4 (DIN)
unnamed: D27.2 (DOUT), D28.4 (DIN)
unnamed: D28.2 (DOUT), D29.4 (DIN)
unnamed: D29.2 (DOUT), D30.4 (DIN)
unnamed: D30.2 (DOUT), D31.4 (DIN)
unnamed: D31.2 (DOUT), D32.4 (DIN)
unnamed: D32.2 (DOUT), D33.4 (DIN)
unnamed: IC1.2 (CKo), IC2.5 (CKin)
unnamed: IC1.3 (SDo), IC2.4 (SDin)
unnamed: IC2.2 (CKo), IC3.5 (CKin)
unnamed: IC2.3 (SDo), IC3.4 (SDin)
unnamed: IC3.2 (CKo), IC4.5 (CKin)
unnamed: IC3.3 (SDo), IC4.4 (SDin)
unnamed: IC4.2 (CKo), IC5.5 (CKin)
unnamed: IC4.3 (SDo), IC5.4 (SDin)
unnamed: IC5.2 (CKo), IC6.5 (CKin)
unnamed: IC5.3 (SDo), IC6.4 (SDin)
unnamed: IC6.2 (CKo), IC7.5 (CKin)
unnamed: IC6.3 (SDo), IC7.4 (SDin)
unnamed: IC7.2 (CKo), IC8.5 (CKin)
unnamed: IC7.3 (SDo), IC8.4 (SDin)
unnamed: IC8.2 (CKo), IC9.5 (CKin)
unnamed: IC8.3 (SDo), IC9.4 (SDin)
unnamed: IC10.2 (CKo), IC11.5 (CKin)
unnamed: IC10.3 (SDo), IC11.4 (SDin)
unnamed: IC9.3 (SDo), IC10.4 (SDin)
unnamed: IC9.2 (CKo), IC10.5 (CKin)
unnamed: IC11.2 (CKo), IC12.5 (CKin)
unnamed: IC11.3 (SDo), IC12.4 (SDin)
unnamed: IC12.2 (CKo), IC13.5 (CKin)
unnamed: IC12.3 (SDo), IC13.4 (SDin)
unnamed: IC13.2 (CKo), IC14.5 (CKin)
unnamed: IC13.3 (SDo), IC14.4 (SDin)
unnamed: IC14.2 (CKo), IC15.5 (CKin)
unnamed: IC14.3 (SDo), IC15.4 (SDin)
unnamed: IC15.2 (CKo), IC16.5 (CKin)
unnamed: IC15.3 (SDo), IC16.4 (SDin)
unnamed: IC16.2 (CKo), IC17.5 (CKin)
unnamed: IC16.3 (SDo), IC17.4 (SDin)
unnamed: IC17.2 (CKo), IC18.5 (CKin)
unnamed: IC17.3 (SDo), IC18.4 (SDin)
unnamed: IC18.2 (CKo), IC19.5 (CKin)
unnamed: IC18.3 (SDo), IC19.4 (SDin)
unnamed: IC19.2 (CKo), IC20.5 (CKin)
unnamed: IC19.3 (SDo), IC20.4 (SDin)
unnamed: IC20.2 (CKo), IC21.5 (CKin)
unnamed: IC20.3 (SDo), IC21.4 (SDin)
unnamed: IC21.2 (CKo), IC22.5 (CKin)
unnamed: IC21.3 (SDo), IC22.4 (SDin)
unnamed: IC22.2 (CKo), IC23.5 (CKin)
unnamed: IC22.3 (SDo), IC23.4 (SDin)
unnamed: IC23.2 (CKo), IC24.5 (CKin)
unnamed: IC23.3 (SDo), IC24.4 (SDin)
unnamed: IC24.2 (CKo), IC25.5 (CKin)
unnamed: IC24.3 (SDo), IC25.4 (SDin)
unnamed: JP1.1, Q1.2 (S)
unnamed: R7.1, U2.3 (AISEN)
unnamed: R8.1, U2.6 (BISEN)
unnamed: R9.1, U2.8 (nFAULT)
unnamed: R12.1, U4.5 (VIO)
unnamed: R12.2, U4.9 (~RSTb)
unnamed: U3.33 (XTAL2), Y1.3
unnamed: U3.34 (XTAL1), Y1.1

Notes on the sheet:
2.7-10.8V
Motor Driver and Motor Power
USB to UART Bridge
Atmega2560
Speaker
Servo-Connectors
Range sensor connector
WS2812B LED Matrix
Buttons
Potentiometer
Cap between Pin 99 and 100
Caps between Pins 31/32 and 61/62
ICSP

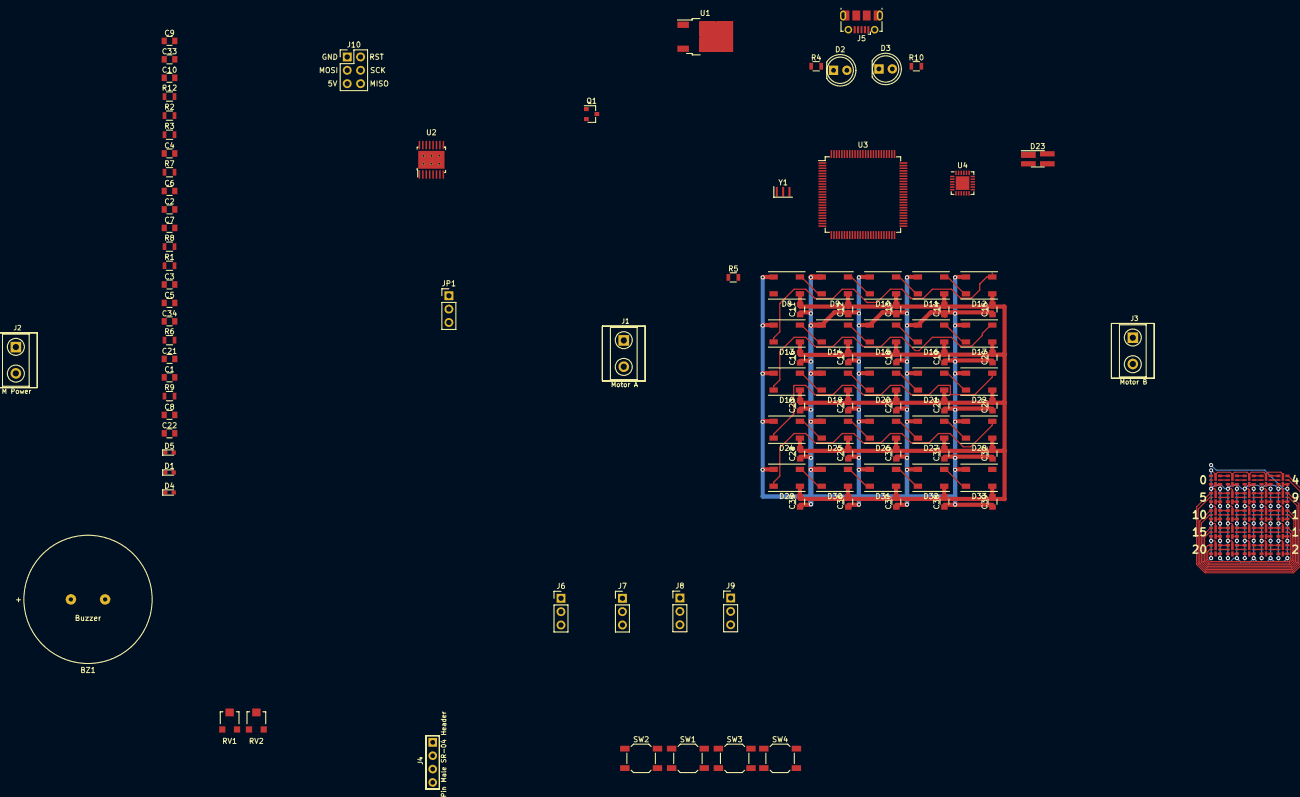
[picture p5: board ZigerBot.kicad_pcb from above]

Board: 4 copper layers, 130 parts (0 on the bottom side), 127 nets.

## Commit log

2018-10-06 Added Inspiration and Changed to On-Board Atmega and Serial-to-TTL chip
2018-10-08 Adds folder hierarchy and first kicad comit
    [ZigerBot.kicad_pcb, ZigerBot.sch]
2018-10-08 Erweiterte Ordnerstruktur
    [ZigerBot.kicad_pcb, ZigerBot.sch]
2018-10-08 and again changing the folder hierarchy
    [ZigerBot.kicad_pcb, ZigerBot.sch]
2018-10-11 PCB erweitert
    [ZigerBot.csv, ZigerBot.kicad_pcb, ZigerBot.sch]
2018-10-14 Added all peripheral components
    [ZigerBot.sch]
2018-10-14 PCB changed
    [ZigerBot.kicad_pcb, ZigerBot.sch]
2018-10-28 Updated Package Info
    [ZigerBot.kicad_pcb, ZigerBot.sch]
2018-10-30 LED-Matrix routed
    [ZigerBot.kicad_pcb, ZigerBot.sch]
2018-10-31 changed pin mappings in README
    [ZigerBot.kicad_pcb, ZigerBot.sch]
2018-11-01 Added ICSP Header, Connected all peripherals to Atmega2560, updated README.md
    [ZigerBot.kicad_pcb, ZigerBot.sch]
2019-04-03 Groundplane, Missing GND and VCC connection
    [AtmegaBreakout.kicad_pcb, AtmegaBreakout.sch]
